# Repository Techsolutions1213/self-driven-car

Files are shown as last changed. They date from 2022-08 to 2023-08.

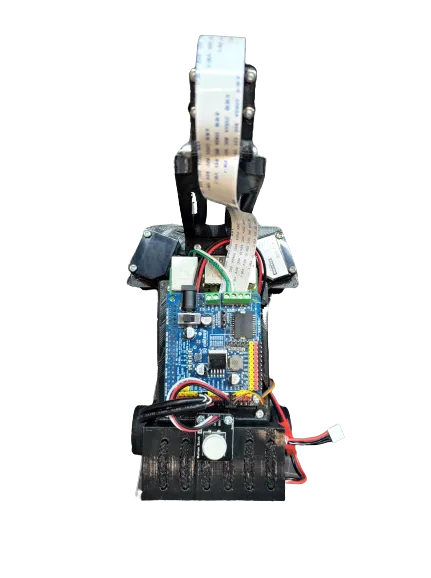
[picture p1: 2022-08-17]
images/top_view.png

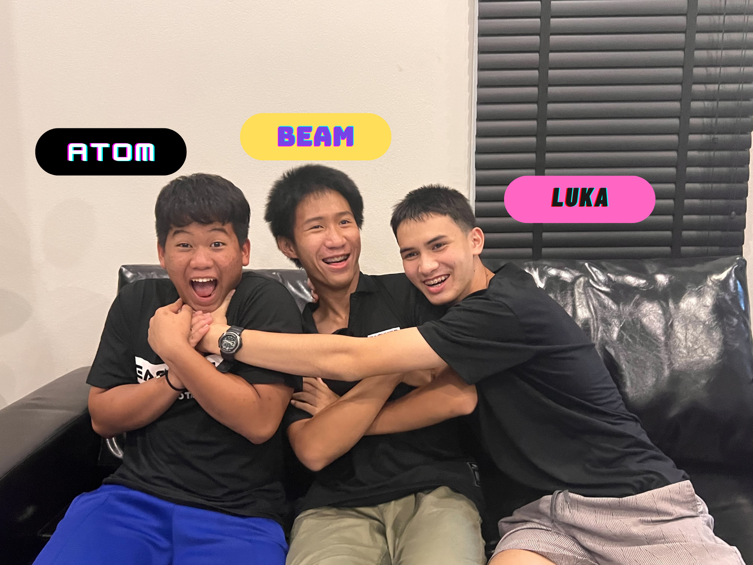
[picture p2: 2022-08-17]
images/team_fun.png

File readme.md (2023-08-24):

# World Robot Olympiad Thailand 2023
<div align="center">
    
</div>

## Table of Contents
- [1. Team introduction](#1-team-introduction)
- [2. Robot Design](#2-robot-design)
- [3. Program structure and Techniques used](#3-program-structure-and-techniques-used)
- [4. Problem solving & Solutions](#4-problem-solving--solutions)
- [5. Discussion](#5-discussion)
- [6. Summary](#6-summary)
- [7. Special thanks](#7-special-thanks)

## 1. Team introduction

### About Us

We are from Team **EasyKids-Janjam**. Our members are **Petch**, **Luka**, and **Tonkla**. We met each other at our robotics institution, **EasyKidsRobotics**. Despite each of us coming from different schools, we still came to meet each other through our love and passion for robotics at this very institute. We've been given the opportunity to develop programming and robotics skills together, enabling us to understand the strengths of each team member. This has allowed us to efficiently allocate tasks based on individual aptitudes
like the saying "Put the right man on the right job." As a result, we've achieved successful outcomes in our projects and integrated our efforts for this competition.

### Our roles

**1. The Mechanic (Petch):**
He is the one who conceives the robot's design, then troubleshoots, and assembles the robot. He tackles issues that arise during the assembly of the robot. He conceptualizes the assembly process from the very beginning, including the initial design, all the way to the latest iteration.

**2. The Programmer (Luka):** 
He will be responsible for designing the robotics program, testing the written code, and rectifying any errors in the program. Moreover, he will work on refining the program to achieve the best possible outcomen.

**3. The Documentarian (Tonkla):** 
He will be responsible for documenting various tasks undertaken, including assembly processes, errors encountered, lessons learned, and information about equipment usage.
____

## 2. Robot Design
### Initial Design

<div align="center">
    
</div>

- **The chassis:** The chassis is derived from a 1/28 scale RC car, which has been modified to incorporate a customised steering kit. Instead of using a linking mechanism, we connect the servo directly to the steering axle. This way we can gain more range of motion, faster steering response for stability and it forces both wheels to turn at the same angle. 

	As for our drivetrain, we chose to use the rear wheel drivetrain to achieve the maximum steering angle possibl, allowing for tighturns
	in confined spaces. The propulsion system is placed at the front to prevent interference between the steering and propulsion components during operation.

- **The Base:** Our initial plan was to pursue a minimalist-style robot and utilize 3D-printed parts as sparingly as possible. Therefore, we decided to use the lidar sensor as our front base, while the electronics at the back are supported by a pillar part.

- **Main Board/Processor:** The brains of the robot is the Raspberry Pi which is coupled with the Derivmotor Shield tp ensure safe power distribution to components, safeguarding the Raspberry Pi from potential wiring errors. In layman's terms, the Derivmotor Shield manages the electronic components, while the Raspberry Pi issue commands to the robot

- **Sensors:** 
	
	- **The Lidar** module is integrated as a control component, collaborating with a camera system. The camera system is designed to rotate, allowing for a comprehensive view in all directions. All these subsystems are coordinated and controlled by a Raspberry Pi, which also manages the motor control.

		The reason for using the Lidar sensor is because it can detect objects, walls, and elements in a 360-degree field of view with high accuracy. However, there are a few limitations to using the lidar. Firstly it cannot be used at very high speeds. This may hinder us in the qualifiers when the goal is to go as fast as possible. Secondly the layout has black edges which does not reflect light well and goes against the mechanics of the lidar.

	- **The camera** is connected to a servo motor, so that we can extend of camera's field of view. The reason for using a rotating camera is that it can capture images and objects from all directions, allowing you to select the desired orientation for object detection.

	- **Gyroscope** is helps improve the stability of object and line detection in OpenCV.But the Gyroscope is that we couldn't find the required library.

- **The power supply:** The power supply system employs a 3-cell battery connected to a step-down converter to lower the voltage to 11.2 Volts. This adjustment ensures a consistent power supply, safeguarding the electronics
against potential power shortages. Subsequently, this voltage is directed to the Deriv Motor Shield, which regulates the voltage to prevent any damage to the Raspberry Pi. The 5V power output from the Deriv Motor Shield serves to power both the motor and ultrasonic components.

### Final design
<div align="center">
    
</div>

In this version, we removed the lidar and gyroscope. The lidar was replaced by the ultrasonics at the front. After some testing with the lidar it occured to us that the lidar didn't perform very well because of the dark edges on the field. We also wanted our robot to be fast so we opted to change the lidar to ultrasonics instead.

Ultrasonics use sound waves for distance detection   

The reason for choosing Ultrasonic over Lidar is that while Lidar can detect objects, walls, and elements in a 360-degree field of view with high accuracy, it may struggle to detect dark-colored surfaces effectively. This limitation led to the decision to switch to Ultrasonic technology. Ultrasonic sensors utilize sound waves for detection, which doesn't significantly affect their ability to detect objects, walls, and elements. This makes Ultrasonic sensors more suitable for accurate object detection and obstacle avoidance, regardless of the color of the surfaces.

The reason we removed the Gyroscope is that we couldn't find the required library, which caused us to waste time. We decided to address the issue by removing it.

## 3. Program structure and Techniques used

### Program structure
We have gained inspiration for coding from the 'Doggy Car' project, such as the practice of code modularization.
### Color Detection

Match that color to the orange and blue lines and the red and green objects.By grasping which color that represents, we will be able to measureThe HSV values of orange-blue-yellow with this red begin to decompose into the following colors. Then write the program if you know what color.is any color all the time the motor.To turn and go forward starting from the line we hold the orange and blue to count the lines.how many rounds It will allow us to complete three laps.and the part of capturing red and green objects in order to know what color Red should turn right and green should turn left.

- H(Hue): This determines the type of color, such as red, green, blue, and so on. Adjusting the Hue value changes the color in a circular manner (color wheel), starting from red and looping back to red again.

- S(Saturation): This represents the intensity or vividness of a color. Higher Saturation values result in more vibrant colors, while lower values make colors appear more muted.

- V(Value): This defines the brightness of a color. Adjusting the Value value changes the brightness without altering the base color.

### The PID Controller 

The PID controller is a tool for monitoring and adjusting values based on system feedback. so that the lessons match the target results by calculating the difference between
the target value and the current state of the process. Then use this difference to make adjustments using three main parts: 

- P adjusts the value up and down according to the closeness of the error value.
- I accumulates past error values. and eliminate consecutive outliers due to external disturbances. 
- D Predict future errors by considering the rate of change.

of error prevents the target from being exceeded. By tuning these components, the PID controller can be adjusted to be more stable and reasonable in the situation.
various

### Threading

Threading refers to the simultaneous execution of multiple tasks in a program, where each task is divided into thread that works for each part
But all threads share resources, for example, by dividing complex computational tasks into threads so that they can run simultaneously. or using separate threads to work
Frequency I/O (Input/Output) with the same anti-wait in a single thread.

## 4. Problem solving & Solutions
### Qualifiers

Ultrasonic sensors on the left and right sides are used to detect objects and walls. Then, the left and right ultrasonic sensors are input into a PID control loop. This is done to make the robot walk straight, stay centered, and maintain the most stable posture possible.

### Finals
For the final round, we used the principles of OpenCV to detect objects and lines for the purpose of implementing a PID equation to perform color detection on the object.

## 5. Discussion
To enhance the technique, various strategies can be employed, such as fine-tuning the ultrasonic sensors for improved accuracy and stability, implementing OpenCV for optimized performance, and incorporating other techniques to further refine and enhance its capabilities.

## 6. Summary

The modification of a 1/28 scale RC car into a robotic system with a custom 
steering kit, propulsion system, and integrated ultrasonic sensor. 
The Raspberry Pi, step-down converter, and camera system are key components 
of the system's control and functionality. OpenCV enhances the camera's object 
detection capabilities

### What  have learned
learned the importance of mutual assistance and knowledge exchange in 
collaborative projects. You've gained experience in problem-solving and 
design thinking. You've also realized the significance of selecting 
appropriate sensors, managing energy efficiently, integrating components 
effectively, and dealing with the complexities of programming behaviors 
as needed. This experience will serve as a foundation for further exploration 
and development in the fields of robotics and automation.

## 7. Special thanks 🙇‍♂️
We would like to express our gratitude to our parents, teachers, and all the supporters who have been with us throughout this journey. Thank you for your continuous support on this journey.

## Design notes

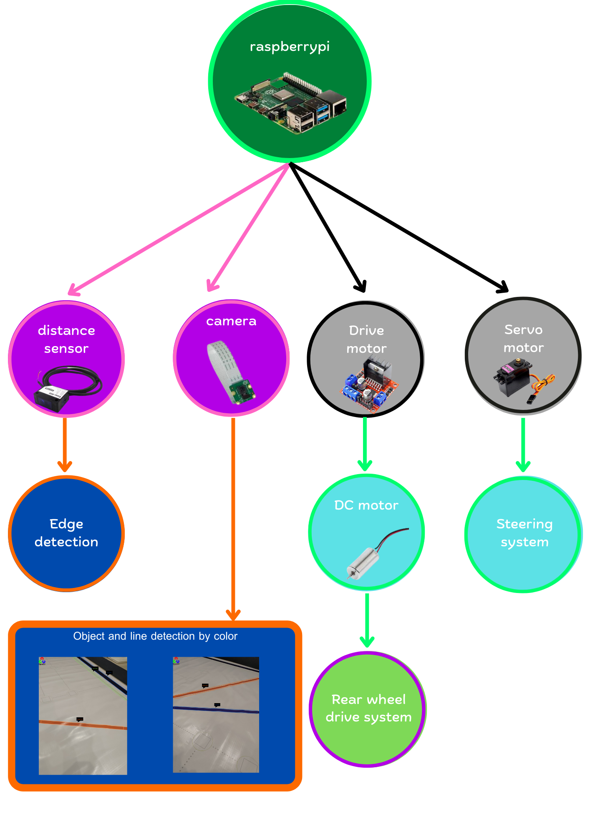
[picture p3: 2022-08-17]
images/diagram.png

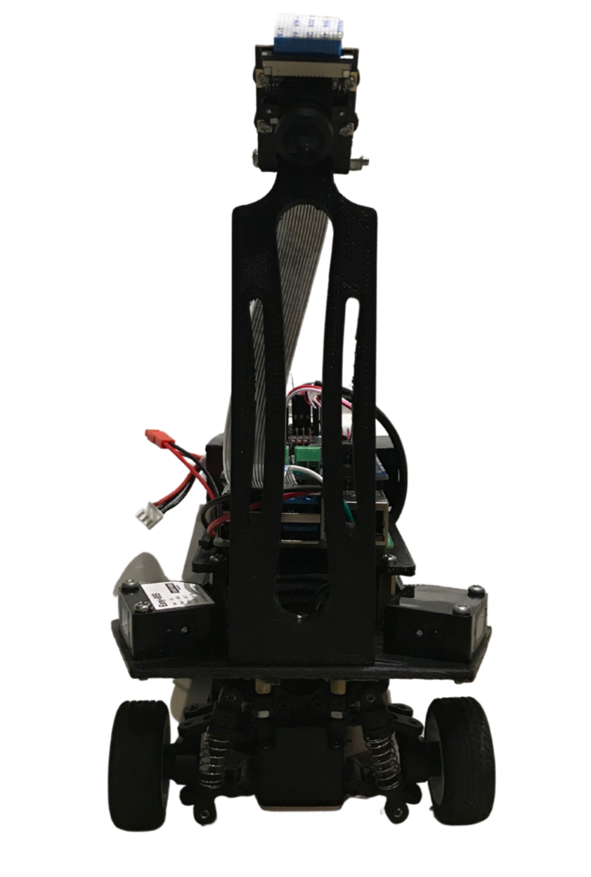
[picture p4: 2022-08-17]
images/front_view.png

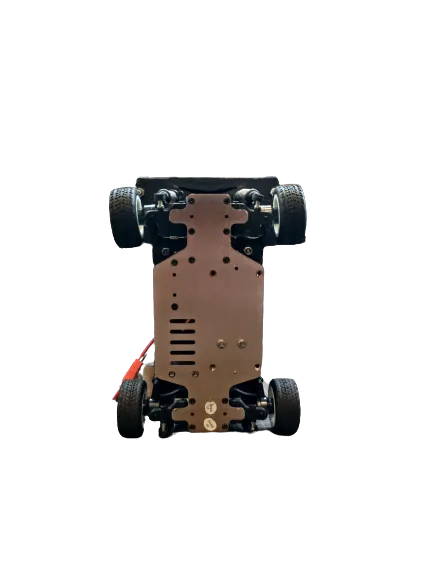
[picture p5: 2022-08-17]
images/bottom_view.png

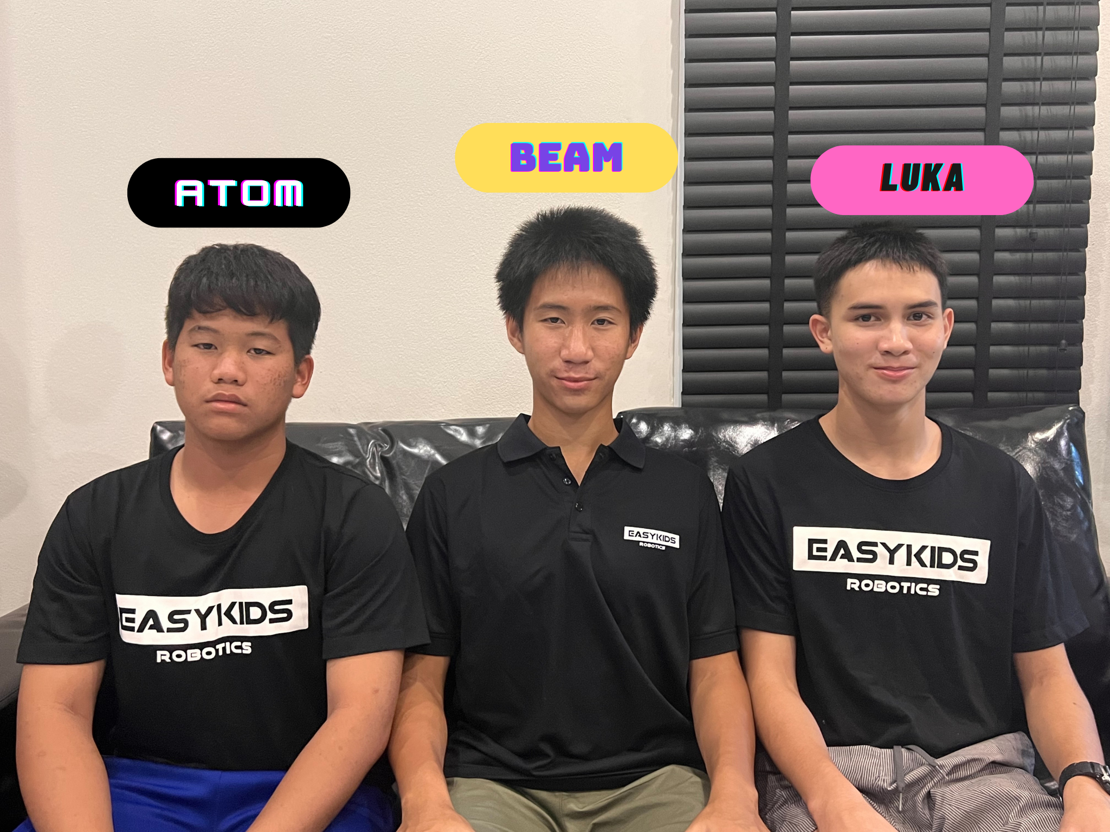
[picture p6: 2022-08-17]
images/teaem_official.png

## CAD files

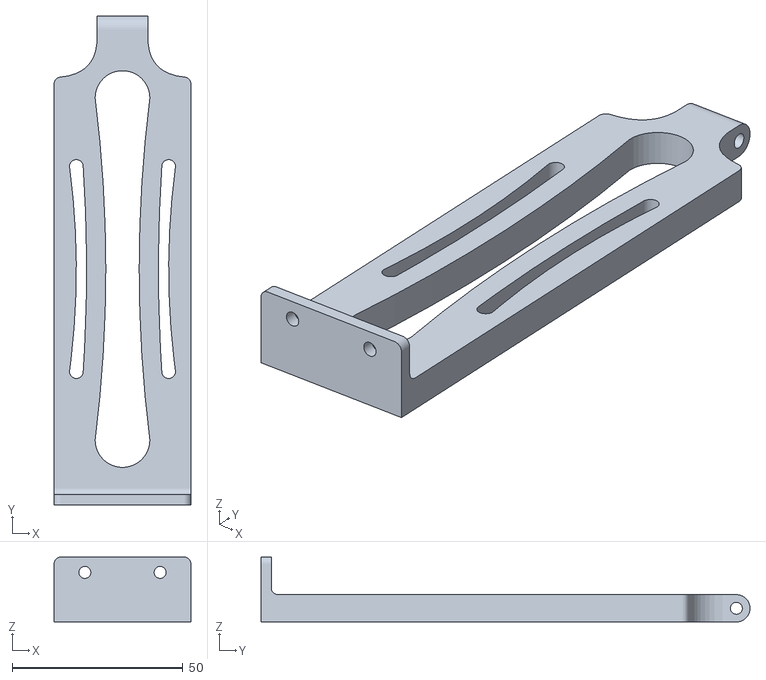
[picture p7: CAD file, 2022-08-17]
models/camera_stand_v2.STL
40.0 x 143.0 x 19.0

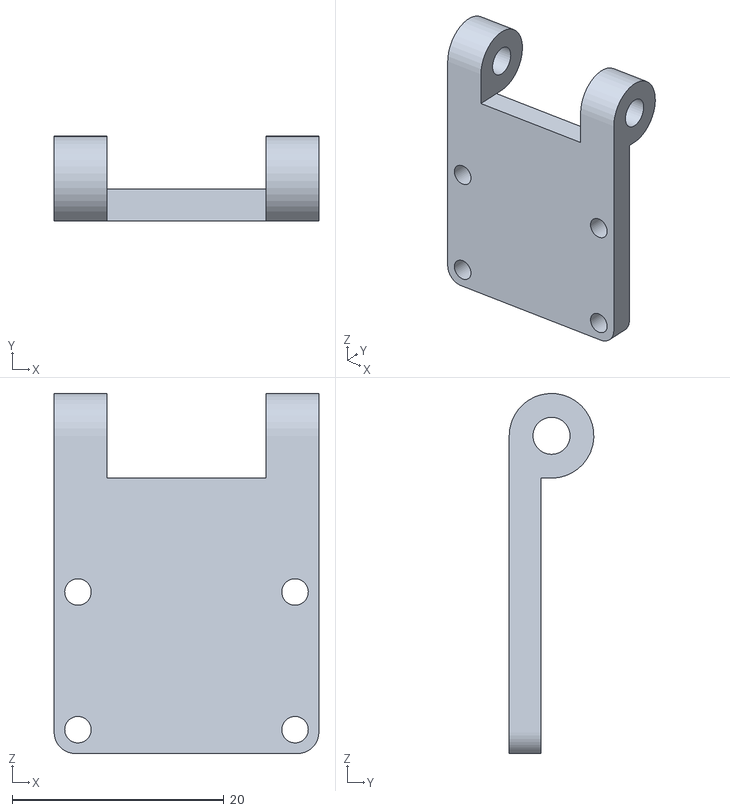
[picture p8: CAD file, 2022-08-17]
models/camera_holder.STL
25.0 x 7.99 x 34.0

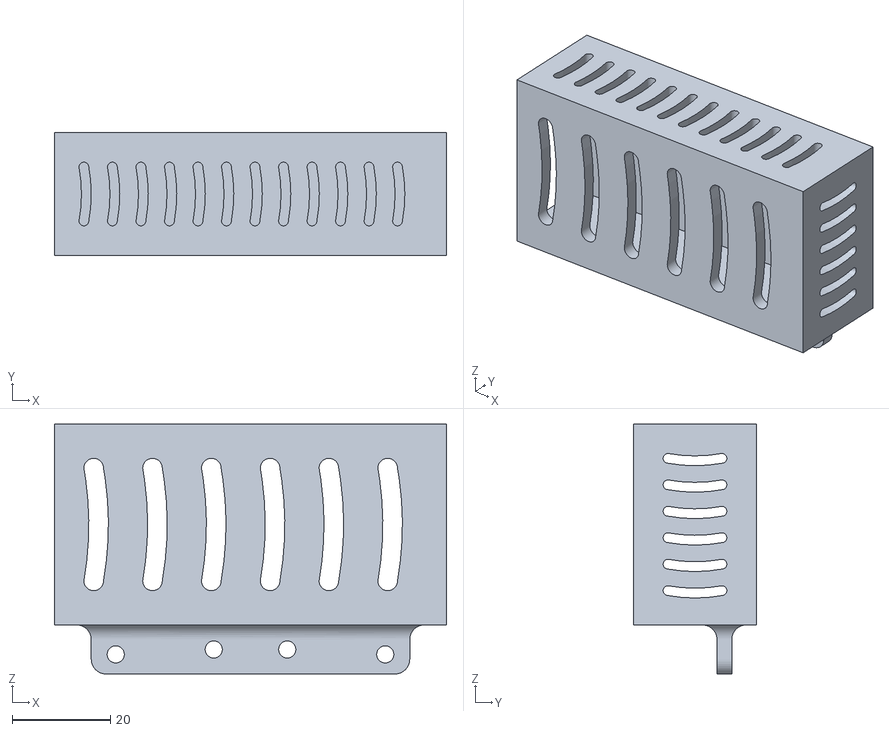
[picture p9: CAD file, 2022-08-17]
models/battery_pack.STL
80.0 x 25.0 x 51.0

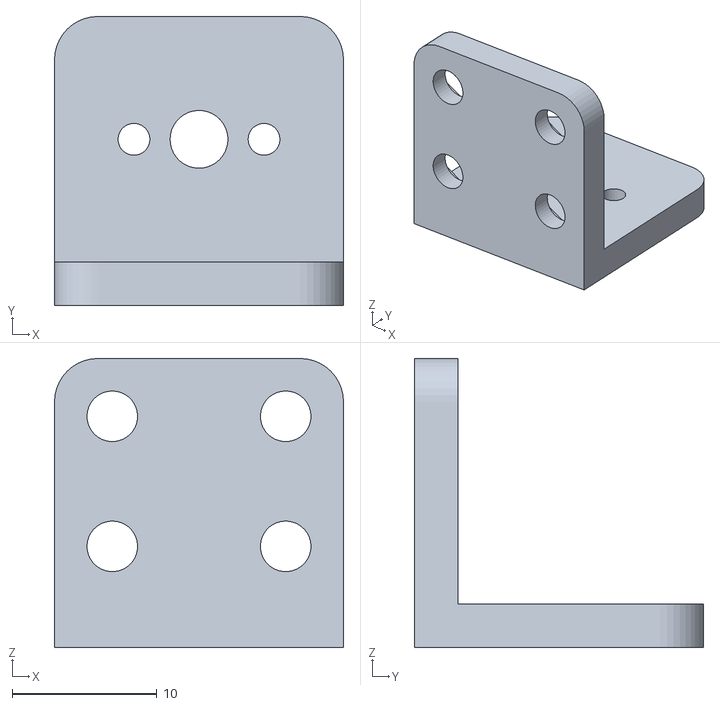
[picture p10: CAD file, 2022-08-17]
models/motor_holder.STL
20.0 x 20.0 x 20.0

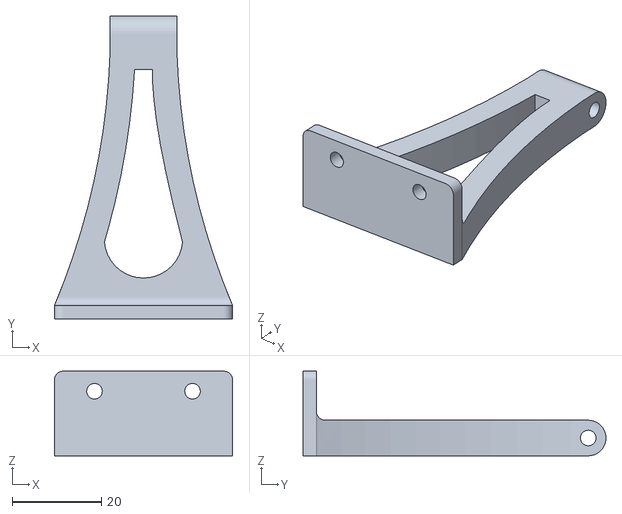
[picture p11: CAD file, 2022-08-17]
models/camera_stand.STL
40.0 x 68.0 x 19.0

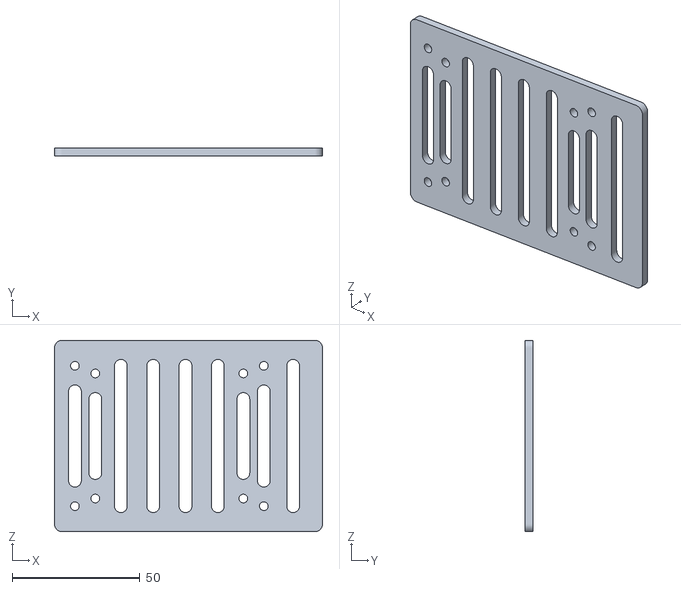
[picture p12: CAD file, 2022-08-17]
models/rpi_base.STL
105.0 x 3.00 x 75.0

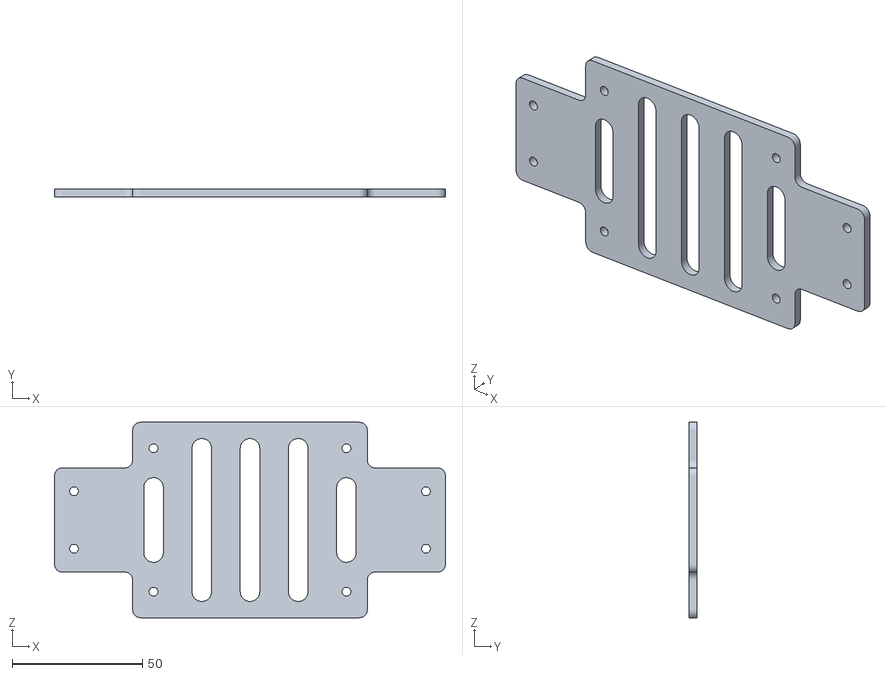
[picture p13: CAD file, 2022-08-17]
models/base.STL
150.0 x 3.00 x 75.0

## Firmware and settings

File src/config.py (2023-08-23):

class config():

# ~~~~~ GPIO CONFIGURATION ~~~~~ #

    WIRE_GPIO = 2
    BUTTON_GPIO = 25

    # Motors #
    IN1 = 19
    IN2 = 16
    EN = 13
    MOTOR_FREQ = 1000

    # Servos # 

    SERVO_MIN_ANGLE = 0
    SERVO_MAX_ANGLE = 180

    SERVO_MIN_PULSE_WIDTH = 0.0005
    SERVO_MAX_PULSE_WIDTH = 0.0025

    # Steering servo #
    STEERING_GPIO = 7
    STEERING_LEFT = 50
    STEERING_MIDDLE = 83
    STEERING_RIGHT = 130

    # Camera servo #
    CAM_SERVO_GPIO = 8
    CAM_SERVO_LEFT = 170
    CAM_SERVO_MIDLEFT = 130
    CAM_SERVO_MIDDLE = 82
    CAM_SERVO_MIDRIGHT = 45
    CAM_SERVO_RIGHT = 0

# ~~~~~ CAMERA CONFIGURATION ~~~~~ #

    CAMERA_PORT = 0

    ORANGE_LOWER_BOUND = [4, 91, 69]
    ORANGE_UPPER_BOUND = [15, 182, 160]

    BLUE_LOWER_BOUND = [96, 40, 43]
    BLUE_UPPER_BOUND = [118, 227, 138]

    RED_LOWER_BOUND_1 = [0, 146, 61]
    RED_UPPER_BOUND_1 = [6, 243, 138]

    RED_LOWER_BOUND_2 = [165, 101, 43]
    RED_UPPER_BOUND_2 = [179, 239, 166]

    GREEN_LOWER_BOUND = [54, 101, 49]
    GREEN_UPPER_BOUND = [79, 233, 162]

# ~~~~~ PID CONFIGURATION ~~~~~ #

    MIDDLE_KP = 0.1
    MIDDLE_KI = 0
    MIDDLE_KD = 0.02
    
    BLOCK_KP = 0.35
    BLOCK_KI = 0
    BLOCK_KD = 0.1

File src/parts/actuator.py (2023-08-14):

from gpiozero.pins.pigpio import PiGPIOFactory
from gpiozero import AngularServo
import RPi.GPIO as GPIO

GPIO.setmode(GPIO.BCM)
pigpio_factory = PiGPIOFactory()

class motorController():
    def __init__(self, in1=19, in2=16, en=13, freq=1000):
        GPIO.setup(in1, GPIO.OUT) # In 1
        GPIO.setup(in2, GPIO.OUT) # In 2
        GPIO.setup(en, GPIO.OUT) # En

        self.in1 = in1
        self.in2 = in2
        self.pwm = GPIO.PWM(en, freq)
        self.pwm.start(0)
        
    def setDirection(self, direction: int):
        if direction > 0:
            GPIO.output(self.in1, GPIO.LOW)
            GPIO.output(self.in2, GPIO.HIGH)
        elif direction < 0:
            GPIO.output(self.in1, GPIO.HIGH)
            GPIO.output(self.in2, GPIO.LOW)
        else:
            GPIO.output(self.in1, GPIO.LOW)
            GPIO.output(self.in2, GPIO.LOW)
        
    def setSpeed(self, speed: int):
        if speed > 100:
            speed = 100
        elif speed < 0:
            speed = 0

        self.pwm.ChangeDutyCycle(speed)
        
class servoController():
    def __init__(self, port=7, minAngle=0, maxAngle=180, min_pulse_width=0.0005, max_pulse_width=0.0025):

        self.servo =AngularServo(port, min_angle=minAngle, max_angle=maxAngle, min_pulse_width=min_pulse_width, 
                        max_pulse_width=max_pulse_width, pin_factory=pigpio_factory)
        
    def setAngle(self, angle: int):
        self.servo.angle = angle

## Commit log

2022-08-16 Added camera.py to parts/
2022-08-17 Added models/
    [base.STL, battery_pack.STL, camera_holder.STL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]
2023-08-05 Lidar testing
2023-08-05 Created the lidar class
2023-08-05 Created LidarRun.py for testing
2023-08-12 Fixed bugs in lidar.py
    [lidar.py]
2023-08-12 Created parts/actuator.py
2023-08-12 Updated parts/lidar.py
2023-08-14 Created tests/ultrasonic.py
2023-08-14 Created src/ultrasonic.py and updated other parts
